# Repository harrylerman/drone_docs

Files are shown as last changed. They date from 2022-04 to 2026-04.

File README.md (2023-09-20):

# drone_docs
Documentation for the Pterosoar drone

Documentation includes: 

    Preflight prep guide: quick guide to ensure compliance with the CARs for every drone flight.

    Normal procedures: Required by CARs. Pre-flight, Takeoff, Launch, Approach, Landing procedures.
    
    Emergency procedures: Required by CARs: Control station failure, equipment failure, RPA failure, Lost Link, Flyaway, Flight Termination procedures. 
  
    TC Drone AIM: Fantastic source of knowledge for drone flying and the regs, doc from TC.

    TC CARs Part IX: Drone CARs.

    Flight log: Logbook form.

    Maintenance log: Logbook form.

    Operations Manual: Required by CARs. Sections: General, Description, Limitations, Hazards-Warnings-Protections, Normal/Emergency procedures, Handling-Care-Maintenance, Supplements/Payloads.
    
    Pos-Alt-Verification (for operations in controlled airspace): Verification of lateral/vertical position accuracy.

    Pos-Alt Addendum: Addendum to the above verification for the new F9P module.

    Mapping procedures: Procedures to follow for each drone mapping outing. 

All documents are based on the CARs Part IX; Standard 922 - RPAS Safety Assurance; Advisory Circular AC-922-01; and the submission site for a drone Safety Assurance.

CARs Part IX: https://lois-laws.justice.gc.ca/eng/regulations/SOR-96-433/FullText.html#s-900.01

Standard 922: https://tc.canada.ca/en/corporate-services/acts-regulations/list-regulations/canadian-aviation-regulations-sor-96-433/standards/standard-922-rpas-safety-assurance-ca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

AC-922-01: https://tc.canada.ca/en/aviation/reference-centre/advisory-circulars/advisory-circular-ac-no-922-001

RPA Safety Assurance submission form: https://tc.canada.ca/en/aviation/drone-safety/help-drone-safety-partners-manufacturers/submit-drone-safety-assurance-declaration-overview

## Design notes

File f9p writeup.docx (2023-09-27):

Dual F9P documentation and testing

Motivation

The need for a dual-GPS heading system stems from our attempts to fly in the Arctic during Summer 2022. The drone was very finicky to arm for flight, it kept cycling between the green “Ready for flight” (armable) status and the yellow “Not ready” (not armable) status. Once flying it behaved very erratically – would not maintain position in Position Mode, and drifted rather violently laterally until it crashed into a building.

Subsequent logfile analysis revealed the “Magnetometer Innovation Test Ratio” far exceeded acceptable values.

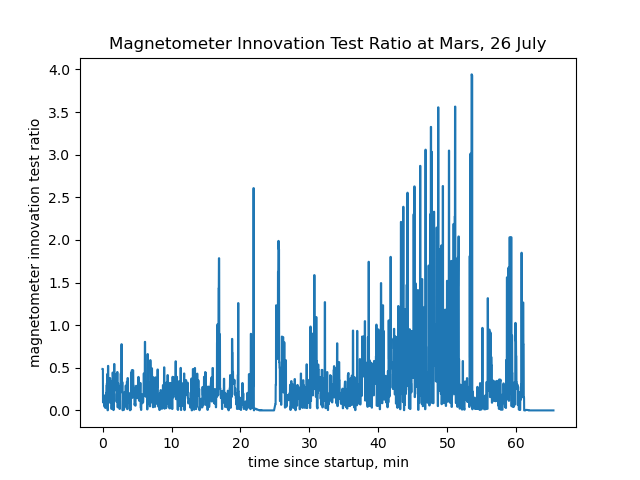
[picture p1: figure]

A brief explanation of this test ratio:

In Kalman filters (https://en.wikipedia.org/wiki/Kalman_filter) which the drone uses for its state estimation (https://docs.px4.io/v1.12/en/advanced_config/tuning_the_ecl_ekf.html), "innovation" has a particular meaning. Here's a wiki link (https://en.wikipedia.org/wiki/Innovation_(signal_processing)) about it. It's similar to a residual, it is the difference between the predicted state at a time t and the actual measured state at time t.

The innovation is the difference between the observed value of a variable at time t and the optimal forecast of that value based on information available prior to time t.

In contrast, the residual is the difference between the observed value of a variable at time t and the optimal updated state of that value based on information available till (including) time t.

The drone calculates its magnetometer innovation and then computes a ratio of the innovation to an "acceptable" level. These quantities are expressed in terms of standard deviations. The acceptable level is set via the "mag_gate" parameter (ctrl-f it here (https://docs.px4.io/main/en/advanced_config/parameter_reference.html)), and is 3 standard deviations by default. The mag ratio should be 0.5 or below at all times (https://mavlink.io/en/messages/common.html):

Under normal operation the innovation test ratios should be below 0.5 with occasional values up to 1.0. Values greater than 1.0 should be rare under normal operation and indicate that a measurement has been rejected by the filter. The user should be notified if an innovation test ratio greater than 1.0 is recorded. Notifications for values in the range between 0.5 and 1.0 should be optional and controllable by the user.

So why were our magnetometer errors so high? It turns out that the magnetic inclination around MARS (https://www.ngdc.noaa.gov/geomag/WMM/image.shtml) is about 88 degrees, ie only 2 degrees off of vertical. That translates to very little signal to the magnetometer. Which motivates the dual GPS system for GPS heading.

Description:

The u-blox F9P GPS module is necessary for dual-GPS heading. Technically the M8P could be used as it supports moving RTK base, but the PX4 firmware would need some hacking to compute the NED components whereas the F9P supplies these components to the FC. We are using two 49g Holybro helical F9P (https://holybro.com/products/h-rtk-f9p-gnss-series)s:

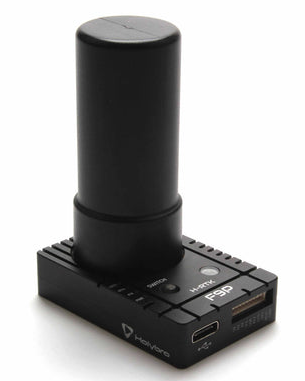
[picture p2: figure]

Dual-F9P system setup

From PX4 site (https://docs.px4.io/v1.12/en/gps_compass/u-blox_f9p_heading.html):

Ideally the two antennas should be identical, on the same level/horizontal plane and oriented the same way, and on an identical ground plane size and shape (Application note (opens new window) (https://www.u-blox.com/sites/default/files/ZED-F9P-MovingBase_AppNote_%28UBX-19009093%29.pdf), section System Level Considerations).

- The application note does not state the minimal required separation between modules (50cm has been used in test vehicles running PX4).
- The antennas can be positioned as needed, but the GPS_YAW_OFFSET (https://docs.px4.io/v1.12/en/advanced_config/parameter_reference.html) must be configured: GPS > Configuration > GPS as Yaw/Heading Source (https://docs.px4.io/v1.12/en/gps_compass/).

In overview:

- The UART2 of the GPS devices need to be connected together (TXD2 of the "Moving Base" to RXD2 of the "Rover")
- Connect UART1 on each of the GPS to (separate) unused UART's on the autopilot, and configure both of them as GPS with baudrate set to Auto. The mapping is as follows:
  - Main GPS = Rover
  - Secondary GPS = Moving Base
- Set GPS_UBX_MODE (https://docs.px4.io/v1.12/en/advanced_config/parameter_reference.html) to Heading (1)
- EKF2_AID_MASK (https://docs.px4.io/v1.12/en/advanced_config/parameter_reference.html) parameter bit 7 must be set (see GPS > Configuration > GPS as Yaw/Heading Source (https://docs.px4.io/v1.12/en/gps_compass/)).
- GPS_YAW_OFFSET (https://docs.px4.io/v1.12/en/advanced_config/parameter_reference.html) may need to be set (see GPS > Configuration > GPS as Yaw/Heading Source (https://docs.px4.io/v1.12/en/gps_compass/)).
- Reboot and wait until both devices have GPS reception. gps status should then show the Main GPS going into RTK mode, which means the heading angle is available.

Note

If using RTK with a fixed base station the secondary GPS will show the RTK state w.r.t. the base station.

In addition to the above parameters, we set the following:

GPS1_config to ‘GPS’

GPS2_config to ‘GPS’

EKF2_mag_type to ‘None’. This removes the magnetometer input from the state estimator.

The heading vector goes from the moving base (connected to GPS 2) to the rover (connected to GPS 1). We have these GPSs aligned back to front, so did not have to configure the GPS_YAW_OFFSET parameter. Here is a page (https://docs.px4.io/v1.12/en/config/flight_controller_orientation.html) I’ve referenced a few times to keep the drone’s reference frame straight in my mind.

Wiring

The rover (front GPS) must connect to GPS1. The moving base (rear GPS) must connect to GPS2.

GPS1 on the Cube Orange is an 8-pin port. GPS2 is a 6-pin port.

Here (https://docs.holybro.com/gps-and-rtk-system/f9p-h-rtk-series/standard-f9p/pinout) is the pinout of the Holybro Helical F9P:

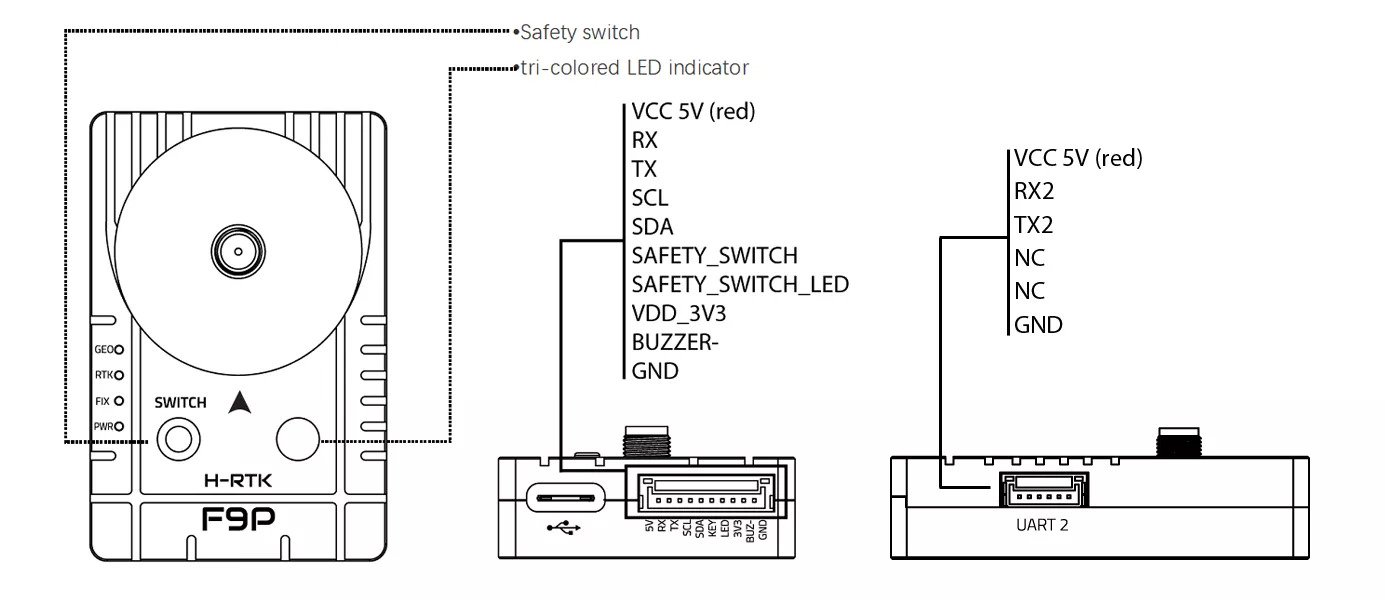
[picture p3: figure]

Note that the main GPS (UART1) port is 10 pins. It is really designed for the newer Pixhawk, like the 6X with the following pinout (https://docs.holybro.com/autopilot/pixhawk-baseboards/pixhawk-baseboard-ports) (perfectly matches the pinout of the Helical):

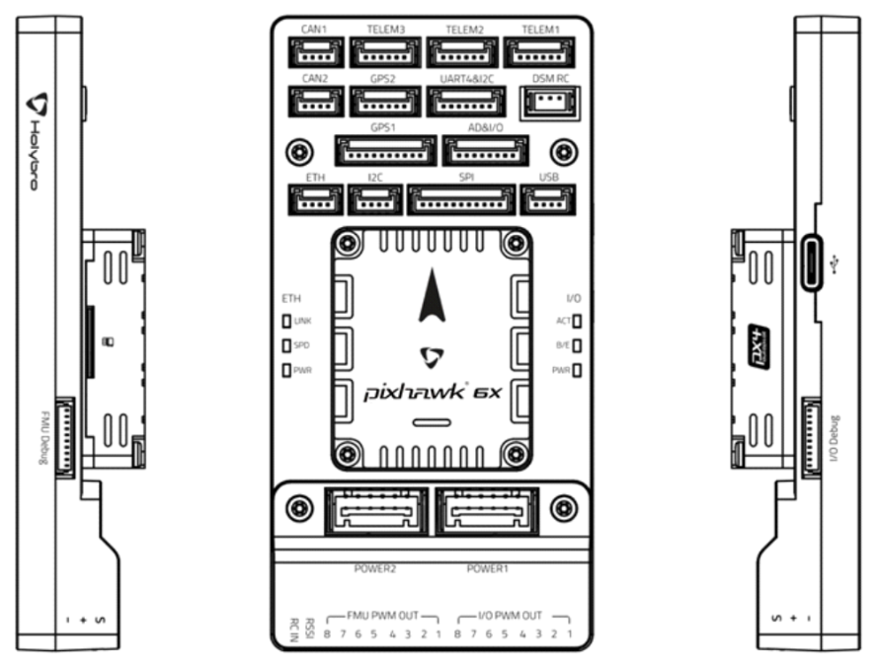
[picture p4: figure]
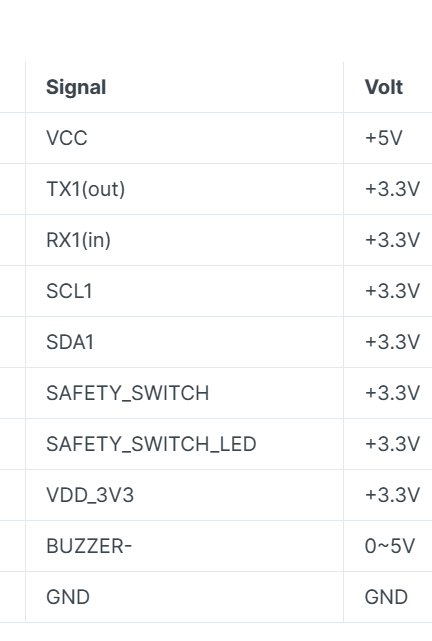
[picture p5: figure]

However, it is still compatible with (https://docs.holybro.com/gps-and-rtk-system/f9p-h-rtk-series/standard-f9p/h-rtk-with-cube-autopilot) the Cube Orange. Here is the Cube Orange pinout for GPS1 and GPS2:

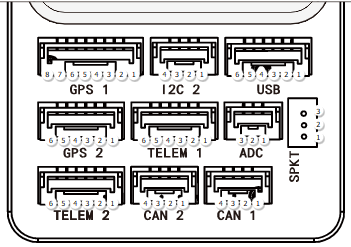
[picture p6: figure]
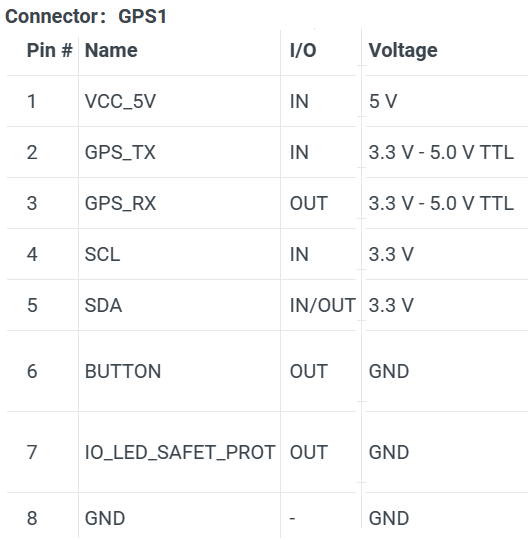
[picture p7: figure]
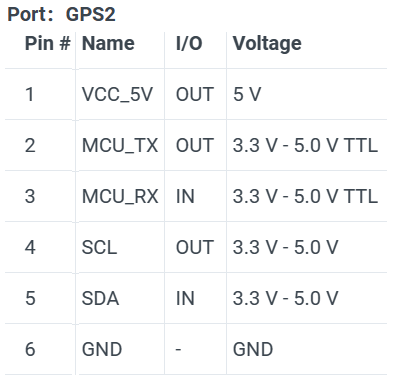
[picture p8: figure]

GPS1 port: Wire the matching connectors from the Holybro to the Pixhawk port (pins 1, 2, 3, 4, 5, 10 from the Holybro to pins 1, 2, 3, 4, 5, 8 on the Pixhawk). The integrated safety switch in the Holybro is not designed for the Cube Orange, it is designed for the 5 or 6x with 3.3V TTL. Also, the Cube Orange has no 3.3 VDD pin, and the buzzer is on the USB connector. So, when connecting the 10-pin Holybro line to the 8-pin Pixhawk port, we leave out the pins for safety switch, safety switch LED, 3.3 VDD, and buzzer (pins 6, 7, 8, 9 on the Holybro side). Would be curious to learn about the decision to move the buzzer from USB to GPS1 between the Cube Orange and 5/6x.

To still use the original safety switch, it can be removed from its default connector by carefully removing the crimped pins 6 and 7 (the two black wires) from the connector, and then de-soldering the splice to pin 1 (5V, red wire). We then insert those crimped connectors into the Pixhawk side of our new GPS line from the Holybro at positions 6 and 7, and splice into pin 1. Or, if that is too much trouble, the button can be disabled via the COM_PREARM_MODE parameter.

GPS2 port: The wiring is similar – do not include pins 6, 7, 8, 9 from the Holybro. GPS2 has no pins for the safety switch so it is not a concern.

UART2 ports: both 6 pin ports, create a line from pin 4 (Tx) of the moving base to pin 5 (Rx) of the rover.

For all of the above, the connector type is JST-GH.

Heading tests on roof

After setting all the parameters and doing all the wiring, we brought the drone up to the roof for some tests. Comparing to a handheld compass, the dual GPS heading seems very accurate, down to a degree or less. This seems to match up with the spec from u-blox (https://www.u-blox.com/en/product/zed-f9p-module) (our baseline is about 67cm):

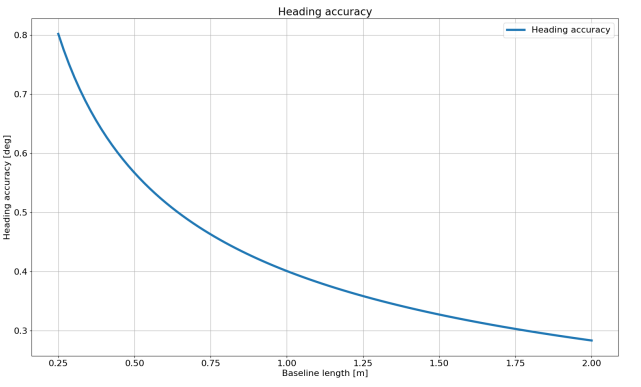
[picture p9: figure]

The resolution seems effectively a degree or less as well. The compass swings very smoothly as the drone is rotated; there is still sensor fusion with the IMUs so this is sensible.

If the drone loses the GPS signal, the heading starts to just swing around in a circle at ~1 deg/sec. But, the drone automatically goes into Altitude Hold mode if it loses GPS, so this isn’t a real danger. There is no indication on the Taranis handheld controller when this happens. There is a text and audio alert from QGC on the laptop.

We wanted to verify that the magnetometer is indeed removed from the state estimator via the EKF2_mag_type parameter. To test this, we waved a magnet next to the drone in the default mode without dual GPS for heading and with the magnetometer enabled. The heading did indeed swing around as the magnet was moved around the Cube Orange. We repeated the test with dual GPS enabled and the magnetometer disabled, and the heading gave no response to the magnet. So hopefully the magnetometer is indeed not included in the state estimator at all.

Hardware mounting

Likely stemming from the ongoing global supply chain issues, 10mm OD carbon fiber tubing of anything greater than 0.5m length is hard to find, and expensive to ship. The Tarot 680 Ironman frame comes with two 10mm OD x 28cm mounting tubes, meant to be held in place by rubber grommets at either end of the frame. They are intended as a gimbal mountpoint for a device such as a camera system. We repurpose these by pulling them out from the drone by approximately 25cm and fixing them in place with 3D-printed mounting brackets. We then 3D-print some mounting platforms for the two GPS units. We had to make sure the mounting platform lowered them below plane of the prop discs.

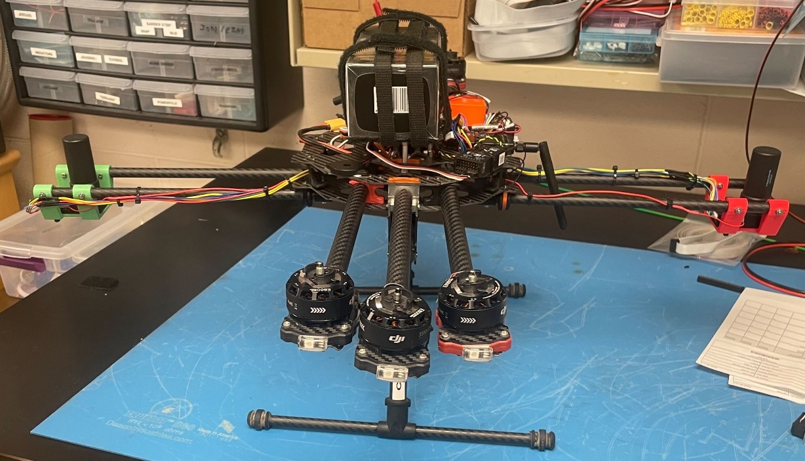
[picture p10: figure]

Drone with dual GPS mounting system. Also visible are the GPS signal lines, and the red line connecting the UART2 ports of the Holybro Helicals.

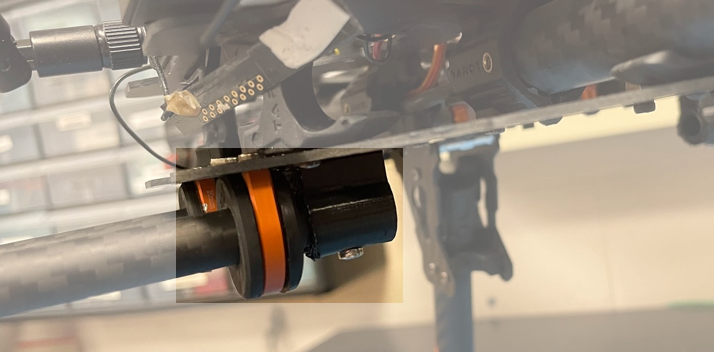
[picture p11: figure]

3D-printed mounting bracket for repurposed Tarot CF tubing (highlighted). The rubber grommets are held by the orange metal brackets.

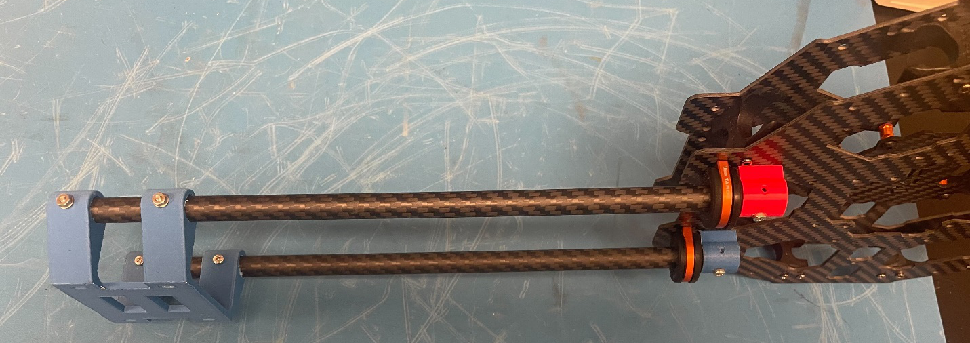
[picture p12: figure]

Some test-printed GPS mounting platforms and CF tubing mounting brackets, included for clarity.

GPS walkaround test for TC

The GPS walkaround test for lateral accuracy verification occurred on March 27, 2023. Details can be found in the memo “Pos-Alt-Addendum.” The GPS system was found to have an accuracy, to a 95% confidence level, of 2.0 m +/- 1.4 m.

First Flight

First flight with the dual-F9P GPS system occurred on March 28, 2023. There were no issues with the drone’s performance – if anything, it seems to fly more stably with the dual GPS system than with the magnetometer (qualitative observation).

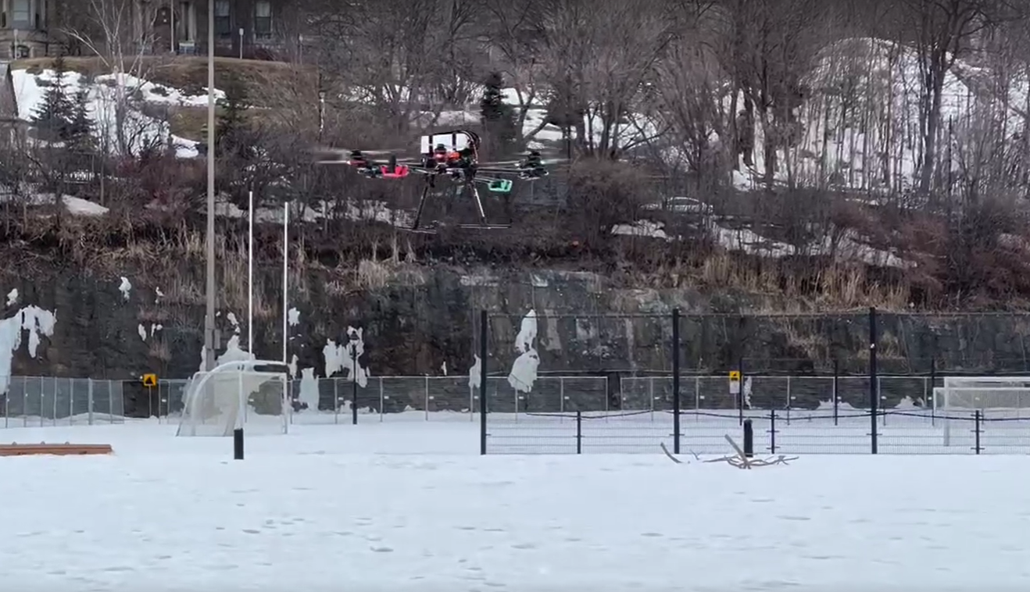
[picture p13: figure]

Coming in for a landing at the conclusion of the first flight of the dual-GPS system.

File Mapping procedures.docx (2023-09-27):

16 Sep 2023

Larry Herman

Drone mapping procedures

Tools to bring on every mapping flight:

- SMA wrench
- Multi-tool
- Digital Multimeter
- Small screwdriver and allen key for drone bolts
- Drone rescue kit
- Spare props
- FieldFox (optional)
- Drone and usual equipment/payload

Items to bring if setting up an LWA and operating without an established ALBATROS station (ie soccer field ops):

- LWA
  - Topper
  - Hardware
  - Petals
  - Central fiberglass supports and flange
  - Central pole
  - Base (ie Xmas tree stand)
- FEE (with optional spare)
- Driver screwdrivers for LWA (2 sizes)
- Readout SNAP box with appropriate RF chain
- Hard drive if not internal to the SNAP box
- RF rescue kit (attenuators mainly)
- GPS antenna
- Batteries with cables (jumper and power cable to readout box)
- Coax cables
  - Riser cables for LWA central pole
  - Long cables from LWA to SNAP box

Setup instructions for flying without an established ALBATROS station (ie soccer field ops):

- Determine location of readout system and crew (ie picnic table)
- Determine location of LWA
  - Can uncoil coax cable and use its length to determine this
- Set up LWA with Xmas tree stand base
  - Includes connecting riser cables to FEE
- Jumper batteries and hook up power cable for the readout box (do not plug in readout box yet)
- Connect GPS antenna to readout box
- Connect hard drive to readout box if needed
- Connect coax cables to LWA riser cables and readout box
- Power on readout box
  - Ensure drone config file is in the new_daq directory and named “config.ini”
  - Ensure drive mounts and dump_baseband and dump_spectra run.
- Power off readout box.

Readout system should now be ready for drone operations.

***From here on the instructions are applicable with or without a full ALBATROS station***

- Perform normal drone preflight procedures.
- Check all accessible SMA connectors on the drone’s payload before and after every flight.

The following are general procedures to perform a complete series of mapping sorties. Flights can be tailored to specific needs of each mapping outing.

- Use the drone to measure the antenna’s lat/lon. Record this.
- Create a flightplan with the drone hovering directly over the antenna for 5 minutes at altitude (ideally 200 ft). Upload flightplan to the drone.
- Power on the transmitter but not the chopper.
- Have the drone takeoff and perform the flight (this is the “cal flight”).
- With the drone hovering over the antenna, power on the readout system and allow to autotune.
- Once autotuning is complete, take control of the drone in position mode and hand-fly to a landing.
- Check ADC bit numbers.
  - May need to tune the RF chains or the drone’s emitter
  - Repeat the cal flight as necessary.
- Power on the chopper.
- Perform the following flights (use saved MARS flightplans as references, flightplans can and should be created ahead of time and the pattern simply moved to the measured antenna position on-site). There will probably need to be 2-3 breaks to charge drone batteries (can take up to 1.5 hours):
  - Star pattern used for a quick check (~6 mins).
  - Center beam raster (~30 mins).
  - Orthogonal center beam raster (~30 mins).
    - Probable battery charge break here (~1.5 hrs).
  - Side-lobe raster (larger pattern but more spaced out, ~30 mins).
  - Orthogonal side-lobe raster (~30 mins).
    - Probable battery charge break here (~1.5 hrs).
  - “Disco ball” and roll/pitch flight: hover the drone at various positions and altitudes, yaw the drone 360 degrees and move the drone laterally to make it roll/pitch, this is to check polarization effects (~5 mins).
  - Re-do the cal flight with the emitter and chopper powered off. This is in preparation for the following drone RFI flight.
  - Drone RFI flight: flight with emitter/chopper powered off to try to gauge the drone’s own RF output. Fly either a simple cross or star pattern as time/battery permits.
- Power down / cleanup.

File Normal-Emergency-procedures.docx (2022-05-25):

Normal Operating Procedures

Ref: 901.23 No pilot shall operate a remotely piloted aircraft system unless the following procedures are established:

- normal operating procedures, including pre-flight, take-off, launch, approach, landing and recovery procedures.

Pre-Flight Procedures:

- Follow the pre-flight planning guide.
- Brief flight crew or visual observers of any duties they are to perform or any other information relevant to the flight.
- Determine the acceptability of actual and developing weather conditions for flight.
- Organize and arrange material and equipment in a manner that makes the items readily available.

Take-off Procedures:

- Complete all preflight procedures and visual inspections.
- Ensure the selected take-off site is clear of obstacles and personnel.
- Command the drone to take-off to an appropriate altitude.
- Ensure the drone lifts off and climbs away in a controlled and stabilized manner.
- Note the take-off time.

Launch Procedures:

N/A, no launch system will be utilized.

Approach Procedures:

- Command the drone to proceed to overhead the intended point of landing.
- Ensure the drone approaches overhead the intended point of landing in a controlled and stabilized manner, and slows so as not to overshoot the landing site.
- Ensure obstacle and personnel clearance as the drone approaches overhead the intended point of landing.

Landing Procedures:

(Recovery procedures: N/A, no recovery system will be utilized.)

- Ensure the intended point of landing is clear of obstacles and personnel.
- Ensure the drone is overhead the intended point of landing.
- Command the drone to descend to the landing site.
- Ensure the drone descends at an appropriate rate in a controlled and stabilized manner.
- Note the time of landing and secure the drone.

Emergency Procedures

Ref: 901.23 No pilot shall operate a remotely piloted aircraft system unless the following procedures are established:

- emergency procedures, including with respect to: a control station failure, an equipment failure, a failure of the remotely piloted aircraft, a loss of the command and control link, a fly-away, and flight termination.

Control Station Failure Procedures:

If the failure is on the part of the ground station (i.e. laptop with QGroundControl):

- Immediately take manual control with the handheld transmitter (i.e. the Taranis).
- Once stabilized, command the drone to altitude or position hold as appropriate.
- Attempt to troubleshoot the ground station failure.
- Assess the ability to continue the flight. If unable, discontinue the flight and land.

If the failure is on the part of the handheld transmitter (i.e. the Taranis):

- Maintain positive control of the drone via the ground station.
- Attempt to troubleshoot the handheld transmitter failure.
- If unable to regain functionality of the handheld transmitter, discontinue the flight and land.

Equipment Failure Procedures:

- Assess the nature of the equipment failure.
- If the pilot and crew determine the equipment failure to be a danger to safety of flight – land immediately (examples of equipment failure that could impact safety of flight: GPS failure, power system failure, radio failure).
- If the pilot and crew determine that safety of flight is not impacted, assess the controllability of the vehicle. If controllability is in doubt – land immediately (examples of equipment failure that could impact controllability: intermittent Holybro or X8R radios, motor failure).
- If the pilot and crew determine that the flight can be continued, assess the impact of the equipment failure on the mission. Alter mission profile as necessary.

Failure of the Remotely Piloted Aircraft Procedures:

- Maintain visual contact with the drone.
- Identify and record the drone’s present position.
- Attempt to maintain control of the drone via any control link (i.e. handheld transmitter or ground station) in any flight mode.
- Attempt to ensure objects and personnel remain clear of potential drone impact.
- Note the position and time of drone impact as applicable.
- Notify the appropriate control facility as applicable.
- File a drone incident report with Transport Canada / TSB as applicable.

Loss of Command and Control Link Procedures:

- Be prepared to take control immediately if at any time the link is restored. Consider landing immediately in this case.
- Maintain visual contact with the drone.
- Identify and record the drone’s present position.
- Attempt to regain control of the drone via any control link (i.e. handheld transmitter or ground station) in any flight mode.
- Select an altitude and power setting appropriate for the lost link situation.
- Attempt to troubleshoot the lost link, being sure to consider both the handheld transmitter and the ground control station.
- Perform “fly-away” emergency procedure as applicable.
- Notify the appropriate control facility as applicable.
- File a drone incident report with Transport Canada / TSB as applicable.

Fly-Away Procedures:

Perform the following tasks without undue delay:

- Identify and record the drone’s present position.
- Identify and record the direction and altitude the drone was last seen travelling.
- Estimate the approximate available flight time that will remain with the fuel/power on board upon arrival at the destination (Example: 15 minutes).
- Comply with “Loss of Command and Control Link” procedures.
- Consider flight termination procedures.
- Without delay contact the appropriate control facility to provide information on the “fly away” as applicable.
- File a drone incident report with Transport Canada / TSB as applicable.

Flight Termination Procedures:

Flight termination is a last-resort emergency option to end the drone flight immediately. All motors will cease operation and the drone will fall uncontrolled from its current position to the ground as the flight computer simultaneously turns off all controllers and sets all PWM outputs to their failsafe values. Note that there is no way to recover from a flight termination once it is triggered – the vehicle requires a hard reset by disconnecting power before it can be used again.

Consider the following before a flight termination:

- The safety of personnel and objects in the vicinity of the drone’s impact site.
- Damage that will result to the drone as a result of the flight termination.
- If flight termination is triggered, file a drone incident report with Transport Canada / TSB as

applicable.

Emergency Contact Information:

Transport Canada Aviation Operations Center 24/7 emergency number (for an imminent and immediate threat to aviation and public safety): 1-877-992-6853

https://tc.canada.ca/en/aviation/aviation-accidents-investigations/emergencies-incident-reporting

Nav Canada 24/7 Flight Operations number (for immediate relay to control facilities): 1-866-WX-BRIEF (1-866-992-7433).

Montreal (CYUL) Tower: 514-633-3312 (Primary) / 514-633-3311

Montreal ACC direct line: 1-800-633-1353.

Quebec FIC direct line: 1-866-541-4105.

VHF/UHF guard frequencies (to attempt to reach any control facility or aircraft in range who may be able to relay information): 121.5/243.0 MHz

Transport Canada drone incident report: https://tc.canada.ca/en/aviation/drone-safety/report-drone-incident

For an incident involving serious injury or death or midair collision, also report to the Transportation Safety Board via phone at 819-994-3741 / 1-800-387-3557 as well as online:

https://www.tsb.gc.ca/eng/incidents-occurrence/aviation/index.html

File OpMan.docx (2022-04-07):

### Pterosoar Operating Manual

### Table of contents

Section 1: General

Section 2: Description

Section 3: Operating limitations

Section 4: Hazards, Protections, and Warning Systems

Section 5: Normal and Emergency Operating Procedures

Section 6: Handling, Care and Maintenance

Section 7: Supplements and Payloads

## Section 1

### General

#### Table of contents

1.1 Introduction

1.2 Warnings, Cautions, and Notes

1.3 List of Definitions and Abbreviations

1.3.1 Abbreviations and Acronyms

1.3.2 Definitions

### 1.1 Introduction

### This Section provides basic data and information of general interest. It also contains definitions or explanations of symbols, abbreviations, and terminology commonly used.

### 1.2 Warnings, Cautions and Notes

The following definitions apply to warnings, cautions, and notes used in this RPAS operating manual:

Warning: An operating procedure, practice, or condition, etc., that may result in injury or death if not carefully observed or followed.

Caution: An operating procedure, practice, or condition, etc., that may result in damage to equipment if not carefully observed or followed.

Note: An operating procedure, practice, or condition, etc., that must be emphasized.

### 1.3 List of Definitions and Abbreviations

#### 1.3.1 Abbreviations and Acronyms

C2: Command and Control

DOP: Dilution of Precision

EMI: Electromagnetic interference

ESC: Electronic Speed Controller

GNSS: Global Navigation Satellite System

GPS: Global Positioning System

GSE: Ground Support Equipment

HITL: Human in the loop

HOTL: Human on the loop

IMU: Inertial Measurement Unit

LiPo: Lithium Polymer

PBM: Power Brick Mini

PDB: Power Distribution Board

QGC: QGroundControl

RPA: Remotely Piloted Aircraft

RPAS: Remotely Piloted Aircraft System

RSSI: Received signal strength indication

RTK: Real-time kinematics

VFR: Visual Flight Rules

VLOS: Visual Line of Sight

#### 1.3.2 Definitions

As may be applicable, add here as needed.

## Section 2

### Description

### Ref: 901.78 A manufacturer that has made a declaration to the Minister in respect of a model of remotely piloted aircraft system under section 901.76 shall make available to each owner of that model of system

### (c) a remotely piloted aircraft system operating manual that includes

### (i) a description of the system

#### Table of contents

2.1 Introduction

2.2 Physical Description of the RPA

2.2.1 Three-View of the RPA

2.2.2 Airframe

2.2.3 Dimensions

2.3 Flight Controls

2.4 Propulsion System

2.4.1 Motor | Propeller | Electronic Speed Control

2.4.2 Battery

2.5 Electrical System

2.6 Avionics System

2.6.1 Navigation

2.6.2 Telemetry

2.6.3 Command and Control Link

2.7 Remote Pilot Station

2.8 Firmware | Software

2.9 Ground Support | Surveillance

### 2.1 Introduction

This Section provides a detailed description of the RPAS and its Systems. Some equipment or payload described may be optional and as such not installed in the RPA. Refer to Section 7 for details of other optional equipment or payload.

### 2.2 Physical Description of the RPA

Airframe Type: Hexacopter

A primarily carbon-fiber construction RPA used for radio science work (mainly antenna calibration) at McGill University.

Built by: Larry Herman, McGill University, Montreal, QC, Canada.

#### 2.2.1 Three-View of the RPA

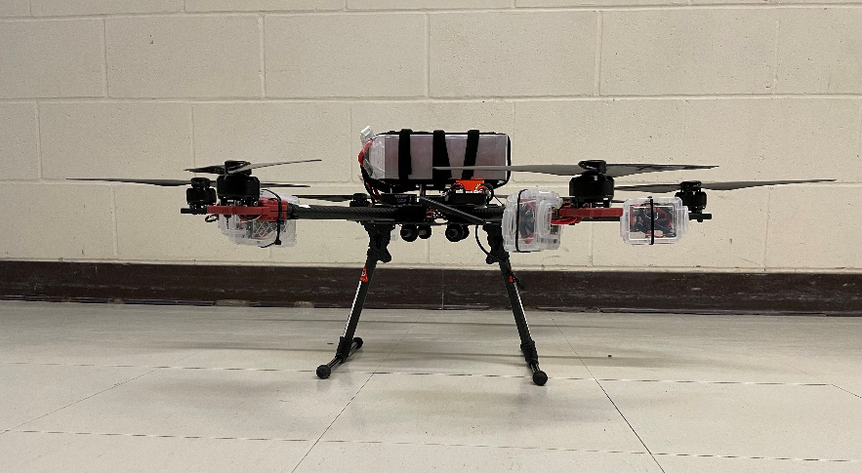
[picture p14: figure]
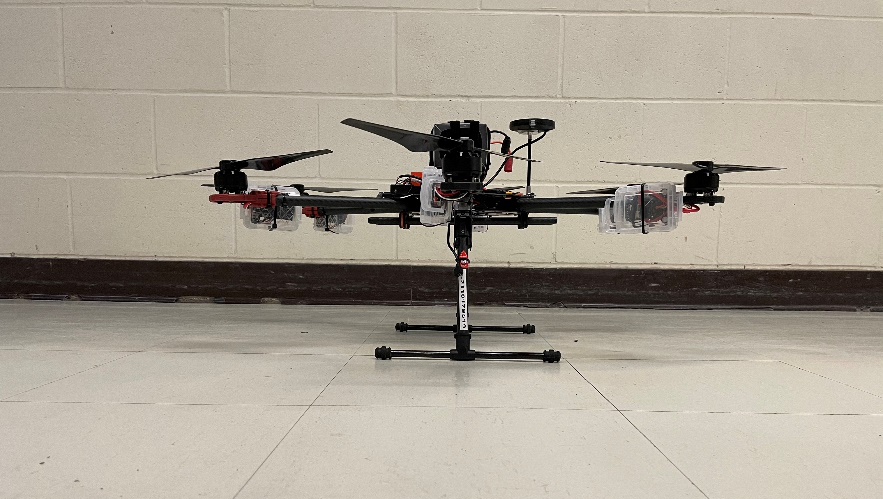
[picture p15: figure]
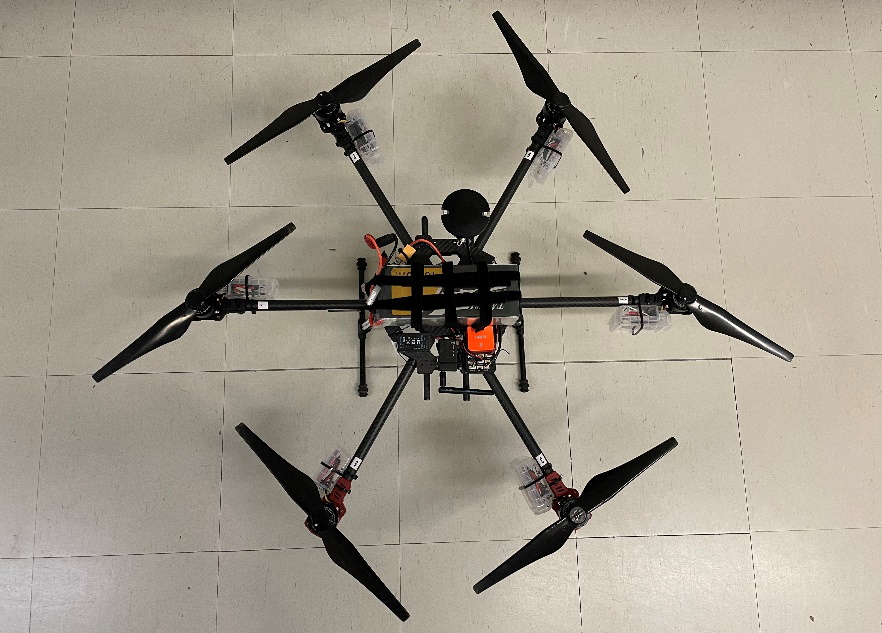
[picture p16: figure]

#### 2.2.2 Airframe

#### Pterosoar incorporates a Tarot Iron Man 680 carbon-fiber frame.

#### 2.2.3 Dimensions

Overall Dimensions: 1015mm x 1015mm x 330mm

Important Dimensions:

#### Motor-to-motor diameter: 685mm

#### Height from ground to lower rods: 180mm

#### Height from ground to top of frame: 220mm

Propeller diameter: 13in

### 2.3 Flight Controls

Pterosoar uses a FrSky Taranis X9D Plus 2019 handheld controller for manual control. For automated control, a groundstation consisting of a laptop running QGroundControl communicates with the RPA via a telemetry system. The method of flight control is conventional: the Pixhawk Cube Orange flight controller varies each motor’s speed to produce the total required torque and thrust to achieve the desired attitude, altitude, and velocity.

### 2.4 Propulsion System

#### 2.4.1 Motor | Propeller | Electronic Speed Control

Motors

Number of Motors: 6

Motor Manufacturer: DJI

Motor Model Number: 3510H

Motor Type: Brushless

Motor Power Rating: 420 KV

Propellers

Number of Propellers: 6

Propeller Manufacturer: DJI

Propeller Model Number: 1345S

Number of Blades: 2

Propeller Type: Fixed pitch

Electronic Speed Controls

Number of ESCs: 6

ESC Manufacturer: DJI

ESC Model Number: Inspire 1

ESC Type: PWM

ESC Power Rating: 26V, 20A

#### 2.4.2 Battery

Battery Manufacturer: Tattu

Battery Type: 6S LiPo

Number of batteries required for flight: 1

Number of spare batteries required (available) on site: Mission-dependent

See Section 3.7 for battery limitations.

#### 2.5 Electrical System

The Pterosoar 6S LiPo battery has a maximum voltage of 3.3V – 4.2V per cell. The battery connects directly to a Power Brick Mini (PBM) power supply via AS150 and XT60 connectors. The PBM supplies full battery voltage to the Power Distribution Board (PDB), and stepped-down 5V power to the Pixhawk Cube Orange flight controller. The PDB supplies electrical power to the motors and ESCs. The flight controller supplies electrical power to all other components.

### 2.6 Avionics System

The primary component of the Pterosoar avionics system is the Pixhawk Cube Orange flight controller. Internal Pixhawk sensors include 3 accelerometers, 3 gyroscopes, 1 compass, and 2 barometric pressure sensors. All other flight-related sensors and radios connect directly to the Pixhawk.

Key features of the Pixhawk:

32bit STM32H743ZI (32bit ARM Cortex M7 (https://en.wikipedia.org/wiki/ARM_Cortex-M), 400 MHz, Flash 2MB, RAM 1MB)

32bit STM32F103 failsafe co-processor

14 PWM / Servo outputs (8 with failsafe and manual override, 6 auxiliary, high-power compatible)

Abundant connectivity options for additional peripherals (UART, I2C, CAN)

Redundant power supply inputs and automatic failover

External safety switch

Multicolor LED main visual indicator

High-power, multi-tone piezo audio indicator

microSD card for high-rate logging over extended periods of time

Below is a diagram of the Pixhawk Cube Orange with all other flight-related components connected. These components are discussed in more detail elsewhere in this Section.

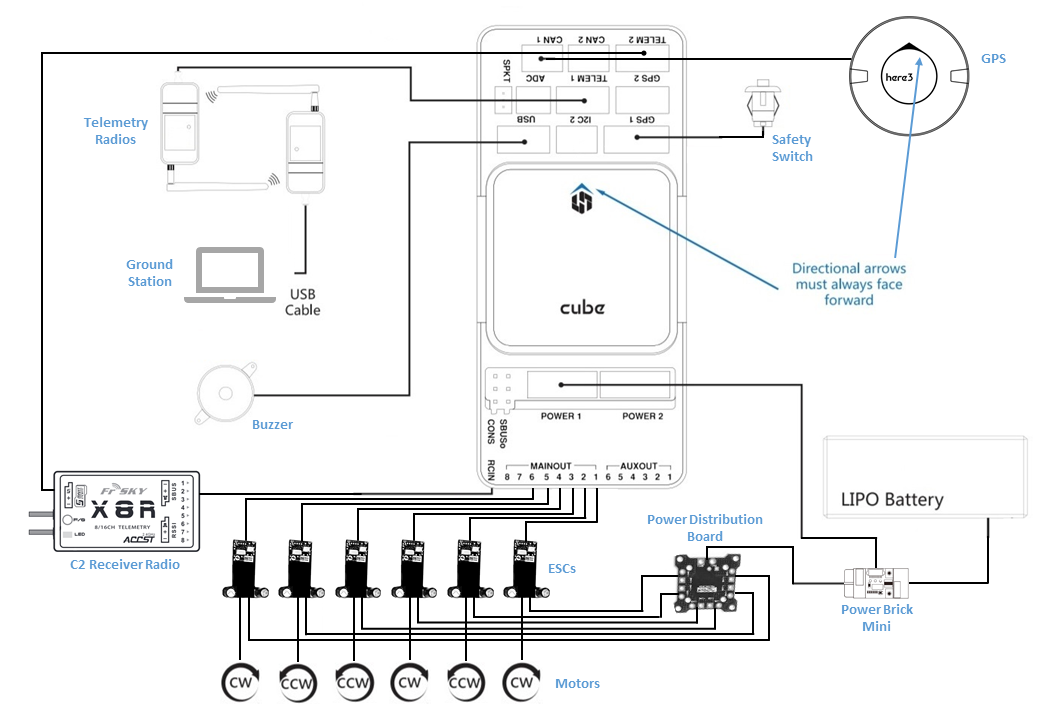
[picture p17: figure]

All sensors and antennas are mounted directly on the central platform, with the exception that one blade antenna from the X8R radio is mounted on arm #1.

#### 2.6.1 Navigation

The Pixhawk Cube Orange flight controller also functions as the autopilot. It is a digital, solid-state system that accepts pre-programmed flight plans uploaded from QGroundControl. It controls the RPA via the conventional flight control system, varying motor speeds to produce the desired torque and thrust to control attitude, altitude, and velocity.

The Pixhawk employs an Estimation and Control Library (ECL) which utilizes an Extended Kalman Filter (EKF) algorithm to process sensor inputs and compute the position state of the RPA. Sensors incorporated into the EKF state estimation include the GPS, IMU, magnetometer, and internal barometric pressure sensor.

Pterosoar’s navigation system includes two separate GPS systems.

The primary GPS system is the Here3 GPS. In the default mode, with a 3D lock the Here3 has an accuracy of +/- 2.5m in any direction. When using the base station for RTK performance, the accuracy is +/- 0.025m in any direction.

The secondary GPS is the Radiolink M8N GPS SE100. The M8N has an accuracy of 0.5m.

#### 2.6.2 Telemetry

Pterosoar uses Holybro SiK Telemetry V3 radios. Telemetry is streamed to the laptop base station running QGroundControl.

Specifications:

Output power: 100mW

Operating frequency: 915MHz

Firmware: Open-source SIK

2.6.3 Command and Control Link

Control via the laptop base station running QGroundControl, as well as wireless flightplan upload for autonomous operation, is conducted via the 915MHz telemetry radios.

Manual control is conducted via the FrSky Taranis X9D Plus SE 2019 handheld controller. Specifications:

Output power: 32mW

Operating Frequency: 2.4GHz

Firmware: Open-source OpenTX

The Taranis X9D and the RPA communicate via a FrSky X8R radio. Specifications:

Output power: 39mW

Operating Frequency: 2.4GHz

Firmware: FrSky ACCST D16

2.7 Remote Pilot Station

The groundstation uses QGroundControl on a laptop with standard keyboard and trackpad. The health and status of the RPA is displayed at the top of the main screen. Navigation information, including a real-time depiction of the RPA on a map, and flight plan information is the main element of the home screen of QGC, as shown below.

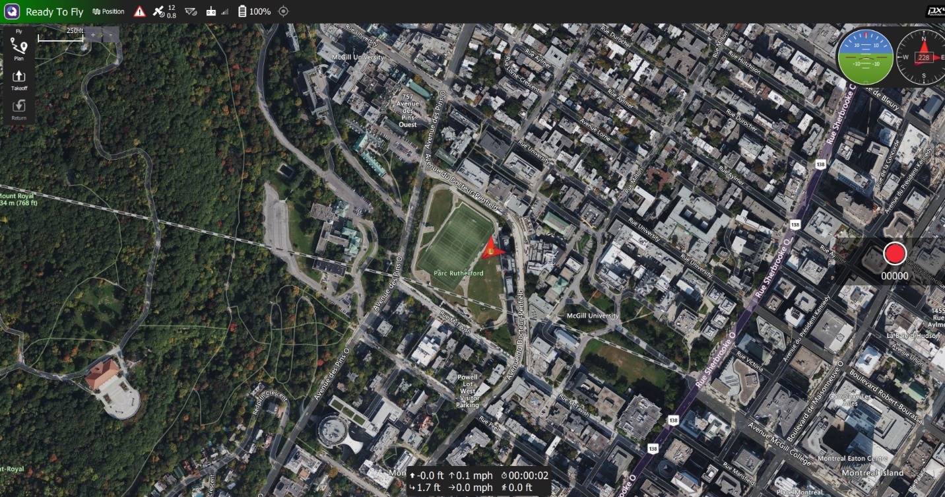
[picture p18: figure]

The Taranis X9D controller has the following switch layout:

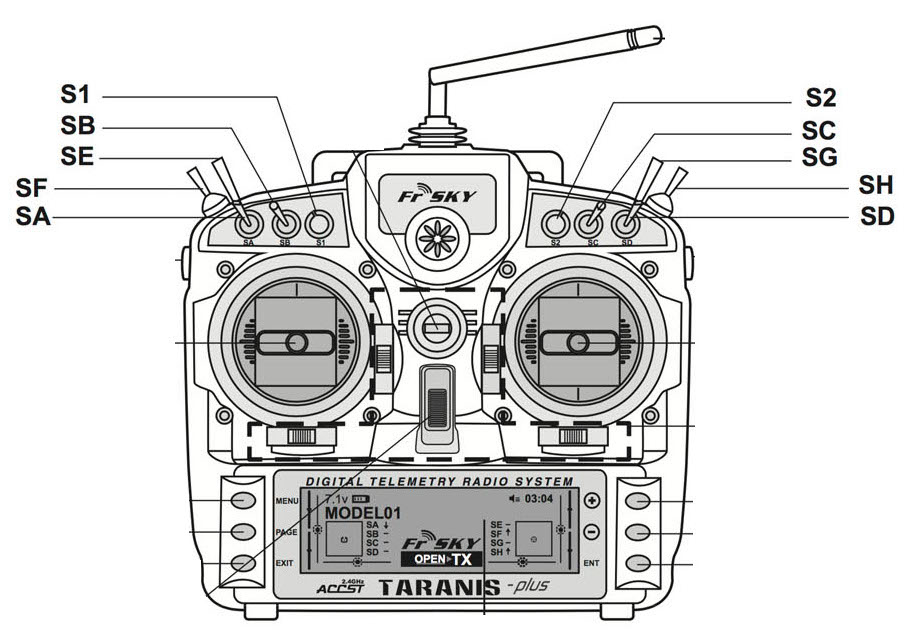
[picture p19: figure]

The controller is configured such that the left stick controls thrust and yaw, and the right stick controls lateral motion (Mode 2).

The primary flight mode switch is SA, and it’s 3 positions are assigned to Altitude (Alt Hold) (up), Position (Pos Hold) (middle), and Mission (Auto) (down). When SC is up, it overrides to Manual mode (this may only be for testing). Moving SE to middle/down will override to Return (RTL). Moving SF to down will override to Land. SC middle/down, SE up, and SF up are all inactive positions.

The main telemetry screen of the Taranis X9D has been configured to show the following information:

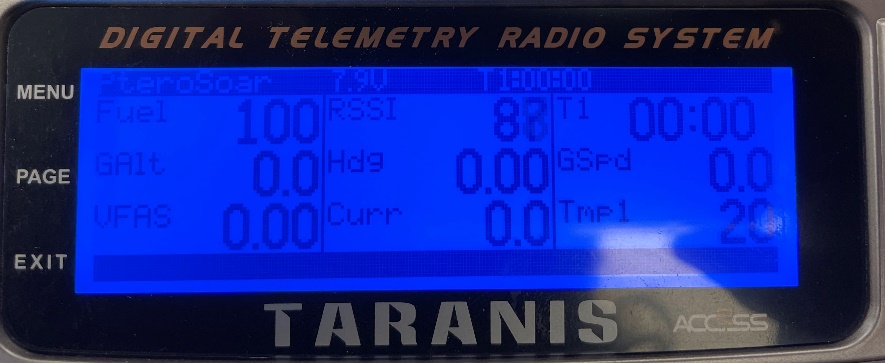
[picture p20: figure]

### 2.8 Firmware | Software

### QGroundControl: Version 4.1.3

### FrSky Taranis X9D: OpenTX version 2.3.12

### Pixhawk: PX4 version 1.12.3

### Holybro SiK telemetry radio: SiK version 2.1

### FrSky X8R radio: ACCST D16 version 2.1.0

### Here3 GPS: version 1.6

### 2.9 Ground Support | Surveillance

No specific GSE is required for the Pterosoar. The RPA must be flown within visual LOS.

## Section 3

### Operating limitations

### Ref: 901.78 A manufacturer that has made a declaration to the Minister in respect of a model of remotely piloted aircraft system under section 901.76 shall make available to each owner of that model of system

### (c) a remotely piloted aircraft system operating manual that includes

(ii) the ranges of weights and centers of gravity within which the system may be safely operated under normal and emergency conditions and, if a weight and center of gravity combination is considered safe only within certain loading limits, those limits and the corresponding weight and center of gravity combinations,

(iii) with respect to each flight phase and mode of operation, the minimum and maximum altitudes and velocities within which the aircraft can be operated safely under normal and emergency conditions,

(iv) a description of the effects of foreseeable weather conditions or other environmental conditions on the performance of both the system and the pilot

#### Table of contents

3.1 Introduction

3.2 Weight | Center of Gravity Limits

3.2.1 Weighing Procedures

3.2.2 Weights

3.2.3 Center of Gravity

3.3 Altitude Limitations

3.4 Velocity Limitations

3.5 Weather Limitations and Effects on System and Pilot

3.6 Kinds of Operation

3.6.1 Operations in Controlled Airspace

3.6.2 Modes

3.7 Battery Limitations

3.8 Range and Endurance Limitations

3.8.1 Battery

3.8.2 Command and Control Link

### 3.1 Introduction

This Section includes operating limitations which are necessary for the safe operation of the RPAS, its motors, standard equipment and standard payload. All information and limits in this Section apply to both normal and emergency conditions.

Warning: All limitations given in this Section must be complied with for all operations.

Note: Refer to the Supplements, Section 7 of this operating manual for information regarding specific equipment or payload.

### 3.2 Weight | Center of Gravity Limits

To obtain the performance, flight characteristics, and safe operation described in this RPAS operating manual, the RPA must be operated within the permissible weight and center of gravity limitations specified in this Section.

### 3.2.1 Weighing Procedures

For weighing, the RPA should be placed in the normal ground position in the center of the scale.

#### 3.2.2 Weights

Basic Weight (including battery): 3.82 kg

Maximum Take Off Weight: 6.30 kg

Maximum payload: 2.48 kg

Warning: Exceeding weight limitations may lead to overloading of the RPA structure and cause loss of control of the RPA and/or structural damage.

#### 3.2.3 Center of Gravity

Pterosoar is a hexacopter with very long moment arms relative to the width of the central platform. The moment arm of any motor to the geometric center of the RPA is 342.5mm, compared to the width of the central platform of 175mm. As a result, components of typical drone equipment weights essentially cannot result in a limiting-case balance condition.

The heaviest component is the battery which is mounted on-centerline at the geometric center of the RPA and as such cannot produce an unbalanced condition. The next heaviest component is the Pixhawk Cube Orange which weighs 73g. Any component weighing less than 73g is considered safe to mount to the central platform without encroaching any limiting-case balance condition.

Any payload must be mounted on-centerline of the central platform. Payloads must be attached to the drone in such a manner that they cannot move or swing dynamically (i.e., no pendulum-style payloads that can swing freely). The flight controller has not been tested with such dynamically movable payloads.

Warning: Exceeding the center of gravity limitations reduces the maneuverability and stability of the RPA.

### 3.3 Altitude Limitations

Maximum altitude: 400 ft AGL or 100 ft above a structure when within 200 ft horizontally from the structure.

Maximum base station altitude: 10,000 ft MSL.

Note: During extended operations, the local barometric pressure (i.e. the local altimeter setting) can change significantly. During such operations, update the QNH barometric altimeter parameter or cycle flight controller power prior to each flight.

### 3.4 Velocity Limitations

Maximum horizontal speed: 20 m/s

Maximum takeoff vertical speed: 5 m/s

Maximum landing vertical speed: 1 m/s

Note: The above limits are based on maximum allowable parameters in QGC and demonstrated performance.

Caution: Maneuver speed and Vne have not been measured. Avoid abrupt control inputs.

3.5 Weather Limitations and Effects on System and Pilot

Wind

Wind limitations: 10 kts sustained, 15 kts gusting.

It is expected that operators have a clear understanding of the effect of wind on aviation, and that flying in wind will have operational effects. In automated (HOTL) flight modes including pre-programmed flight path, automated takeoff, automated landing, or RTH, the RPA will fly against the wind to maintain it’s desired position or flight path. The same is true of semi-automated (HITL) modes including position or altitude hold. In manual mode, the operator must be aware of the winds and make the appropriate inputs to counteract them. In all cases, the effects of flight against the wind on battery endurance should be considered.

Caution: In manual flight mode, flight against winds aloft may increase pilot fatigue.

Temperature

Ambient temperature operating range: 0°C to 40°C

Caution: Consideration should be given to the effects of ambient temperature on pilot fatigue.

Air density

Air density is an important factor in rotary-wing aircraft operations as it directly impacts the generation of lift. Consideration should be given to the density altitude at the time of flight. If the density altitude for the given conditions is abnormally high and aircraft performance seems affected (excess thrust required for takeoff or to maintain altitude), consider aborting the flight.

Caution: Also consider the effects of abnormally high density altitudes on pilot fatigue.

Precipitation

Flight in any form of precipitation is prohibited.

Vibration

Vibrations generally result from the operation of the RPA itself. The Pixhawk flight controller includes vibration isolation on two of the IMU's, with a third fixed IMU as a reference / backup.

Icing

Flight is prohibited when icing conditions are observed, are reported to exist or are likely to be encountered along the route of flight. Flight is prohibited with frost, ice or snow adhering to any part of the RPA.

Electromagnetic Environment

Consider the effects of electromagnetic interference (EMI) from nearby sources such as cell towers, microwave radio relays, or Wi-Fi transmitters. If any interference with the telemetry or C2 link is suspected, abort the flight until the interference is eliminated.

It is strongly suggested to know the KP index expected on the day of the flight. This is the index used to express the magnitude of geomagnetic storms. The scale of the KP index ranges from 0 to 9. It is strongly discouraged to fly a drone when the KP index is between 4 and 9 as this indicates a geomagnetic storm. A geomagnetic storm interferes with the drone's GPS positioning.

3.6 Kinds of Operation

RPAS flights are limited to Visual Line of Sight (VLOS) flights, under DAY Visual Flight Rules (VFR) conditions.

Night flight is prohibited.

#### 3.6.1 Operations in Controlled Airspace

Operations in controlled airspace require an advanced drone pilot certificate and filing with Nav Canada.

Required Accuracy

(1) The remotely piloted aircraft system must have a lateral position accuracy of at least +/- 10m while operating within the controlled airspace.

(2) The remotely piloted aircraft system must have an altitude accuracy of at least +/- 16m while operating within the controlled airspace.

Pterosoar has demonstrated that it meets these accuracy requirements. Results of GPS/altitude verification testing are on file.

The following GPS error considerations should be taken into account during flight operations:

Errors. Accuracy is a probabilistic measurement based on assumptions related to the quality and integrity in a constantly changing environment. It is important to understand the errors that may contribute to degradation of accuracy and take these into account as part of the overall design error budget. Examples of sources of errors adversely affecting accuracy are identified below.

Terrain Errors. GNSS signals are also subject to errors caused by the terrain. Terrain masking of the signal, for example by a building or mountain, blocks the antenna on the RPAS from receiving the satellite signal. A GNSS signal reflected by the landscape such that the receiver now receives "additional" signals which can create confusion and may need to be processed out to avoid creating position errors.

Atmospheric Errors. Atmospheric errors are caused by the Ionosphere and the Troposphere, which are both capable of refracting GNSS radio signals. Ionospheric Density is diurnally dependent, which means that it varies with time of day (or night). The density is affected by, among other factors, humidity, temperature and pressure. These variations adversely affects the "signal speed x time" equation built into GNSS position calculations. To correct for these errors, a number of steps are taken. Troposphere errors can be caused by moisture absorbing/refracting signal and cause errors up to 6m. Ionosphere errors can be caused by the atmospheric refraction of the GNSS signals and may be up to 40-60 m by day and 6-12 m at night. These errors can be mitigated by the use of multi-frequency receivers, selection of masking angle, and/or the use of augmentation systems (either ground-based, such as Local Area Augmentation System [LAAS], or space-based, such as European Geostationary Navigation Overlay Service [EGNOS]).

Satellite Errors. These are errors resulting from poor or unexpected geometries related to the positions of the GNSS satellites in reference to an RPAS. Gravitational effects of the Sun and Moon may pull the SV from planned orbital path. Solar Radiation creates EMI prior to the signal hitting the atmosphere.

Geometric Dilution of Precision (DOP). DOP occurs when there is no adequate cross cut in the "fix" (i.e. all satellites are all too closely located to each other). The consequence is that all of the signals are vulnerable to same errors from the atmosphere. Errors can occur in the horizontal (H), the vertical (V) and in time (T).

#### 3.6.2 Modes

With the exception of automated takeoff, the following modes may be engaged via the Taranis X9D controller as described in section 2.7. All settings are configurable via QGC. Position hold is the recommended flight mode for hand-flying. All flight modes are designed for operation with all motors functioning.

Caution: If any motor ceases functioning, land immediately.

Fully-automated (HOTL):

Mission: Vehicle executes a predefined mission/flight plan (https://docs.px4.io/master/en/flying/missions.html) that has been uploaded to the flight controller.

Return to Home: Ascend to safe altitude and return via a direct path to the home location.

Auto takeoff: Vehicle ascends to takeoff altitude and holds position. Triggered via QGC.

Auto land: Vehicle lands at the position where the mode was engaged.

Semi-automated (HITL):

Position Hold: RC mode where roll, pitch, throttle sticks control movement in corresponding axes/directions. Centered sticks level vehicle and hold it to fixed altitude and position against wind.

Altitude Hold: RC mode like Manual mode but with altitude stabilization (centered sticks level vehicle and hold it to fixed altitude). The horizontal position of the vehicle can move due to wind (or pre-existing momentum).

Non-automated:

Manual: RC mode where centered sticks level vehicle (only - position is not stabilized).

### 3.7 Battery Limitations

Use only 6S LiPo batteries with AS150 connectors. Consideration should be given to battery weight vs capacity if replacing the battery.

Battery capacity: 16000mAh

Maximum charge rate: 1C

Maximum discharge rate: 15C

Ambient temperature for battery charging: 0°C to 43°C.

Ambient temperature for battery discharging: 0°C to 60°C.

Warning: Battery exposure to temperatures greater than 60°C for extended periods of time (more than 30 minutes) may result in damage to the battery or a fire.

### 3.8 Range and Endurance Limitations

#### 3.8.1 Battery

The battery will nominally last approximately 25 minutes depending on flight conditions.

#### 3.8.2 Command and Control Link

The C2 link has a published range of 1.5km. Maintaining VLOS will likely require a reduced range.

## Section 4

## Hazards, Protections, and Warning systems

## Ref: 901.78 A manufacturer that has made a declaration to the Minister in respect of a model of remotely piloted aircraft system under section 901.76 shall make available to each owner of that model of system

### (c) a remotely piloted aircraft system operating manual that includes

- (v) the characteristics of the system that could result in severe injury to crew members during normal operations,
- (vi) the design features of the system, and their associated operations, that are intended to protect against injury to persons not involved in the operations,
- (vii) the warning information provided to the pilot in the event of a degradation in system performance that results in an unsafe system operation condition,

#### Table of contents

4.1 Introduction

4.2 Hazards to RPAS crew

4.3 Protections Against Injury to Uninvolved Personnel

4.4 Warnings and alerts

#### 4.1 Introduction

This section describes potential hazards to RPAS crewmembers, design features to protect against injury to persons not involved in RPAS operations, and the RPAS warning and alert systems.

#### 4.2 Hazards to RPAS crew

Electric shock: The maximum battery voltage is 25.2V which poses a minimal shock risk. The PDB is purposefully located at the center of the frame platform and is difficult to reach by hand, so the chance of accidental contact is remote. The battery should be checked for damage or swelling prior to each use, and never short-circuited.

Laceration: Crew members should not approach the RPA on the ground when armed for flight, or at all when motors are spinning. There is a loud buzzer to alert personnel that the drone is armed for flight and should not be approached. The RPA cannot be armed unless the safety switch has been pressed and held for approximately 2 seconds. If there is a preflight delay, the safety switch should be deactivated to prevent inadvertent arming or motor actuation.

Trauma injuries: Crew members should not approach the flightpath of the RPA unless necessary for an emergency or safety concern, and should never stand directly beneath it. Unless required, it is good practice to stay at least 5m laterally from the RPA.

Burns: Crew members should not mishandle the battery. Mishandling the battery can pose a fire risk. Puncturing, short circuiting, or exposing the battery to excessive ambient temperature could cause a fire. Mishandling the battery during charging by selecting the wrong battery type, failing to perform a balanced charge, or excessive charge rate could cause a fire.

Note: See Section 3.7 for battery limitations.

#### 4.3 Protections Against Injury to Uninvolved Personnel

Pterosoar is not intended to fly over or near people and must maintain 100 ft horizontal separation at any altitude from any non-crew member or person uninvolved in its operations.

The flight crew should include visual observers to ensure that uninvolved personal do not approach the flightpath or come within 100 ft of the RPA.

The RPA has configurable failsafe actions. Failsafe actions include: provide a warning, hover in place, return to home, or land in place. The following conditions can be specified to trigger a failsafe action:

Geofencing: Virtual regions within which the vehicle can fly, or in which it is not allowed to fly. The geofence regions are configurable in QGC. Breaching the fence triggers the failsafe action.

Low power: Battery level which triggers the failsafe action is configurable via QGC.

Lost link (C2 or Telemetry): Link loss timeout and failsafe action for either datalink are configurable via QGC.

#### 4.4 Warnings and Alerts

The primary warning system is through QGroundControl. The laptop base station will sound an audio alert and give a corresponding on-screen message of any system degradation. Alerts include but are not limited to low signal strength, low battery, non-responsive motor, GPS degradation, Pixhawk sensor degradation or failure, geofence alert, etc.

Types of alerts include:

Warning Alert: For conditions that require immediate pilot awareness and immediate response;

Caution Alert: For conditions that require immediate pilot awareness and subsequent response; and

Advisory Alert: For conditions that require pilot awareness and may require subsequent response.

Examples of marginal performance alerting includes:

GPS errors including GPS dilution of precision (DOP) when the geometries of available satellites does not provide sufficient coverage to meet navigation precision.

Navigation/Orientation errors such as Inertial Measurement Unit sensor faults/drifts.

Degradations in C2 link bandwidth and responsiveness cause by unknown or uncharacterized sources of interference, indicated by reduced or marginal RSSI.

Most warnings also appear on the screen of the Taranis X9D with corresponding audio cueing.

## Section 5

## Normal and Emergency Operating Procedures

### Ref: 901.78 A manufacturer that has made a declaration to the Minister in respect of a model of remotely piloted aircraft system under section 901.76 shall make available to each owner of that model of system

### (c) a remotely piloted aircraft system operating manual that includes

### (viii) procedures for operating the system in normal and emergency conditions

### See document “Normal and Emergency Procedures” as well as the pre-flight planning guide.

## Section 6

### Handling, Care and Maintenance

### Ref: 901.78 A manufacturer that has made a declaration to the Minister in respect of a model of remotely piloted aircraft system under section 901.76 shall make available to each owner of that model of system

(a) a maintenance program that includes

(i) instructions related to the servicing and maintenance of the system, and

(ii) an inspection program to maintain system readiness;

### (c) a remotely piloted aircraft system operating manual that includes

(ix) assembly and adjustment instructions for the system.

#### Table of contents

6.1 Introduction

6.2 Transport | Storage

6.3 Assembly | Disassembly

6.4 Cleaning and Care

6.4.1 Propeller Care

6.4.2 Battery Care, Storage, and Use

6.5 Scheduled Maintenance

6.5.1 Annual Inspection (example)

6.5.2 500 Hour Preventive Maintenance (example)

6.6 Other Field and/or Shop Maintenance

### 6.1 Introduction

This Section contains the recommended procedures for proper handling of the RPA. It also identifies certain inspection and maintenance requirements which should be followed if the RPA is to retain its original performance and dependability.

### 6.2 Transport | Storage

Pterosoar should be transported in its protective carrying case with sufficient padding. Propellers should be removed. It is recommended to tape off the positive terminal of the battery.

### 6.3 Assembly | Disassembly

The forward and rear motor arms are hinged and lock in the central position for storage, and in the deployed position for flight. The landing gear is hinged and locks in the downward position for flight operations. The propellers incorporate a DJI quick release mounting system and lock in place.

### 6.4 Cleaning and Care

The RPA can be cleaned with a soft cloth and isopropyl alcohol. Ensure the battery is disconnected and the RPA is powered off prior to cleaning.

#### 6.4.1 Propeller Care

Propellers must be checked before each flight for nicks or cracks and installed securely.

#### 6.4.2 Battery Care, Storage, and Use

The battery is charged using HT206 charger. Ensure LiPo battery type and balanced charge are selected. The maximum charge rate is 1C and discharge rate is 15C. Do not exceed 4.2V per cell. If the voltage is less than 3.3V in any cell, the battery must be replaced. For long term storage (over a week), the battery should be charged to 3.8V – 3.9V per cell.

### 6.5 Scheduled Maintenance

#### 6.5.1 Annual Inspection

Test all batteries for capacity.

Upgrade firmware and software to latest revisions.

#### 6.5.2 500 Hour Preventive Maintenance

Disassembly, inspection of components for wear, replace any components as required by manufacturer.

Test all motors and replace if necessary.

Test all batteries for capacity.

Upgrade firmware and software to latest revisions.

### 6.6 Other Field and/or Shop Maintenance

Either the Here3 GPS or the M8N SE100 GPS may be used. The Here3 plugs into either CANbus port of the Pixhawk. The M8N SE100 plugs into the GPS2 port and the I2C port of the Pixhawk.

## Section 7

### Supplements

#### Table of contents

7.1 General

7.2 Radio Payload

### 7.1 General

This Section contains information regarding optional equipment | payload | accessories which may be installed in the RPAS.

### 7.2 Radio Payload

Radio payload is still under development.

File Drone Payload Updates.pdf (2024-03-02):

## Drone Payload Updates

28 February 2024

## Contents

3.3.2 | Timer/counter compare match interrupt service routine (used to set chopping cadence)...9
3.3.3 | Timer/counter input capture interrupt service routine (used to read PWM pulse width) ....9

## 1 Introduction and current hardware

Until now, the PteroSoar drone radio payload has consisted of the following:

Signal source: Leo Bodnar mini precision GPS reference clock

1

Chopper: Analog Devices HMC545 RF switch eval board²

controlled by an Arduino Mega³

Battery: cellphone battery pack from Amazon with two USB-A outputs

Antenna: Aaronia BicoLog 5070⁴

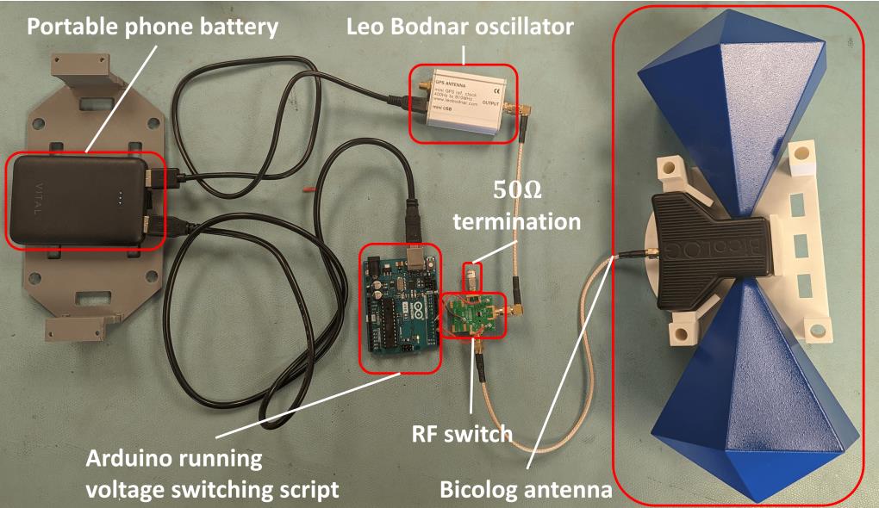
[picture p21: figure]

To switch from a steady-on state to a chopping state, it has been necessary to land the drone and manually change configuration. This is not desired as it needlessly drains battery in the descent to land and climbout back to pattern altitude during the calibration flight at the start of a series of mapping sorties.

The chopping script used on the Arduino has been a simple loop using timeouts to control the GPIO inputs to the HMC545 rf switch. This method of using timeouts is not very accurate, as the Arduino is not perfect at measuring time and the chopper can drift over even short flights. In addition, this setup is needlessly bulky and expensive:

Leo Bodnar cost: CAD $187.75¹

HMC545 eval board cost: CAD $188.68²

Arduino Mega cost: CAD $48.40³

## 2 New Hardware

### 2.1 Overview

Complexity, bulkiness, weight, and cost can be reduced by using a smaller Arduino and a clock generator controlled by the Arduino GPIO. The chopper can be made more accurate and chopping frequency drift minimized by using the internal timer/counter of the Arduino’s processor. Then, the chopping can be implemented by turning on and off the output of the clock generator at a cadence controlled by the timer/counter. There is no need for the RF switch in this configuration, only the Arduino and the clock generator chip. Moreover, by tying the drone’s X8R radio into the Arduino GPIO as an input, we can use the same timer/counter to read the PWM signal and implement radio control of the chopper state (steady on, chopping, or steady off).

In this configuration we have employed an Arduino (Abra) Nano⁵
controlling an Si5351 clock generator chip on a Mikroe-4113 eval board⁶
. Abra is a local electronics store and their Abra Nano is functionally the same as a stock Arduino Nano.

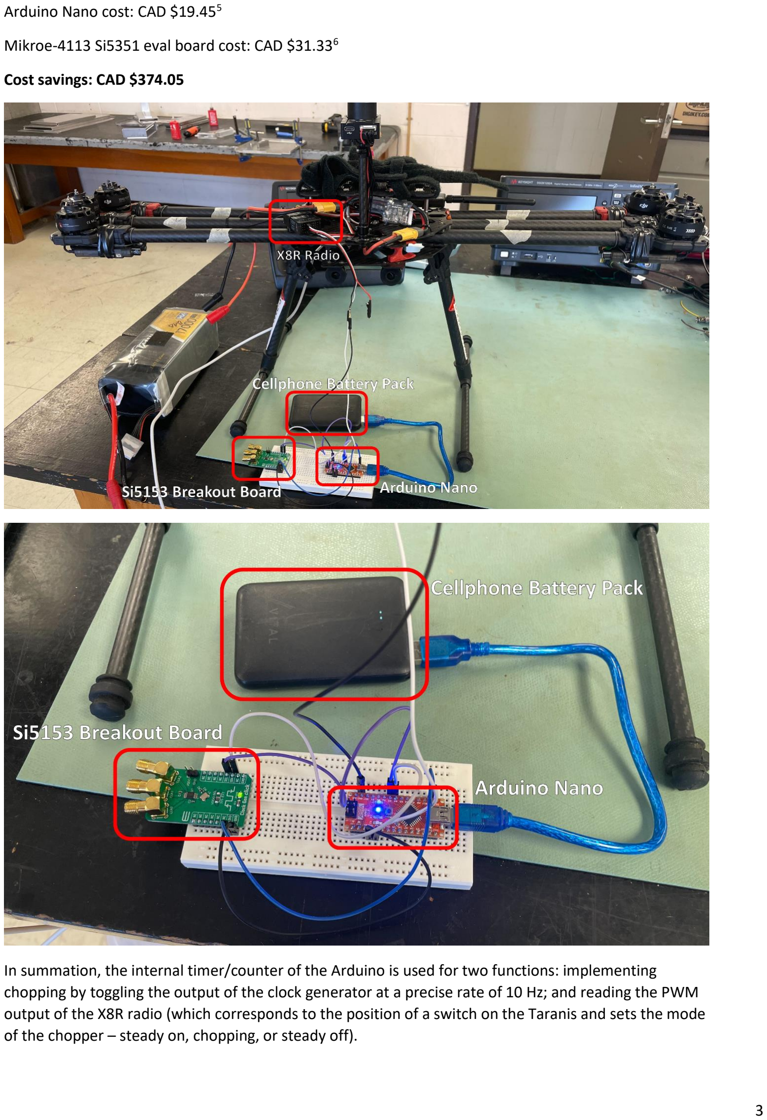
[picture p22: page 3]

Arduino Nano cost: CAD $19.45⁵

Mikroe-4113 Si5351 eval board cost: CAD $31.33⁶

Cost savings: CAD $374.05

In summation, the internal timer/counter of the Arduino is used for two functions: implementing chopping by toggling the output of the clock generator at a precise rate of 10 Hz; and reading the PWM output of the X8R radio (which corresponds to the position of a switch on the Taranis and sets the mode of the chopper – steady on, chopping, or steady off).

### 2.2 Wiring

The Si5153 is controlled via I2C and runs off of 3.3 V. The Arduino’s FTDI USB chip supplies enough current to power the Si5153. For power the 3V3 and GND pins of the Si5153 eval board are connected directly to the 3.3 V tap off of the Arduino and one of its ground pins. If this proves problematic when connected to load, a 3.3 V regulator will be easy to implement. The Arduino Nano’s I2C SDA and SCL pins are pins A4 and A5 by default, and these are wired directly to the SDA and SCL pins of the Si5153 eval board.

The signal and ground pins from output 6 of the X8R radio are connected to pin D8 (the default input capture interrupt pin for the Arduino’s timer/counter – more on that in a bit) and a ground pin, respectively. Output 6 is used because we are using channel 6 (Taranis switch D mapped to channel 6 in the Taranis “Mixes” config page). Channels 1-5 are used for drone control, so channels 6-8 are available for other uses such as the chopper.

Taranis “Mixes” config page, note CH6:

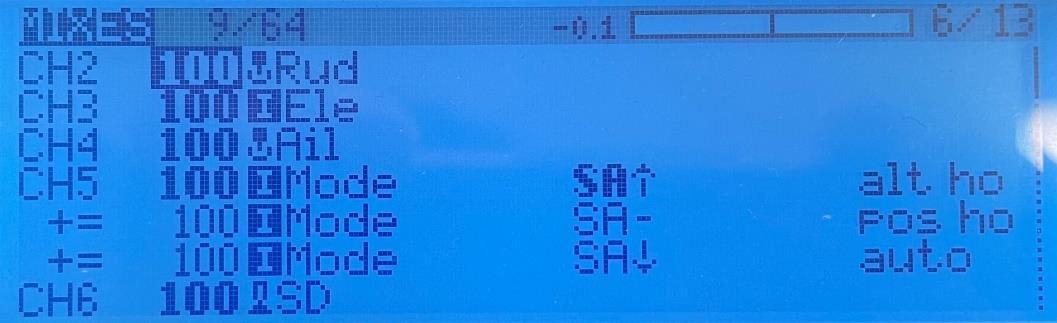
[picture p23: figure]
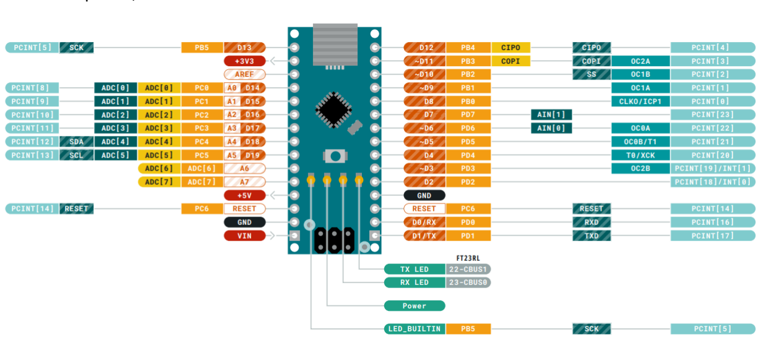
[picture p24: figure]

Arduino Nano pinout, for reference:


Here we can see the I2C SDA and SCL pins on A4 and A5. We can also see the pins concerning the timer/counter:

Output compare pins OC1A and OC1B on pins D9 and D10

Input capture pin ICP1 on D8

The 3.3 V tap off and ground pins are also easily identified.

## 3 Arduino code

### 3.1 Setting up the Si5153 clock generator

The Si5153 has two PLLs and three outputs. To have three different output frequencies, two outputs would need to share one of the PLLs.

Each PLL is set with a multiplier from the default clock speed of 25 MHz. Then each clock output can have two different dividers to set an output frequency.

In integer mode, the two PLL multipliers can have values of 15 to 90. The first clock divider (called multisynth divider) can have values of 4, 6, or 8. The second divider (called additional R divider) can have values of 1, 2, 4, 8, 16, 32, 64, 128. SiLabs recommends integer mode to avoid clock jitter, though fractional settings are also available.

SiLabs puts out some configuration software to help optimize the combinations of PLL multipliers, multisynth dividers, and R dividers for whatever set of output frequencies one desires.

There are two Arduino libraries for the Si5153: one from Adafruit⁷ (https://www.arduino.cc/reference/en/libraries/adafruit-si5351-library/)

, and one from Etherkit⁸ (https://www.arduino.cc/reference/en/libraries/etherkit-si5351/)
. The Adafruit
library gives a bit more intuitive low-level setting of the individual PLL multipliers and dividers. However, the Adafruit library doesn’t have individual on-off control of the three outputs – either all three are on or all three are off.

The Etherkit library does have the ability to set PLLs, but it is functionally “clunky” and is not designed with that kind of manipulation in mind. Instead, the user provides a frequency, and the library determines what multipliers and dividers are necessary to set the desired frequency. The library cautions that if the desire is to set the PLL multisynths and dividers, then the user must keep careful track of the settings to make sure valid multipliers and dividers are used.

Two advantages of the Etherkit library are the ability to turn on and off each of the three outputs individually, and the ability to set the power levels of the three outputs (drive strength from 2 mA or ~ 3 dBm to 8 mA or ~10 dBm, according to Etherkit). Currently, we are using the Etherkit library but the Adafruit version would be simple to implement.

The Si5153 manipulation in the Arduino code is simple. In the setup function, the chip is initialized, the frequency set, and all 3 outputs disabled. As described later, the output of clock 0 is then toggled continuously for chopping or set to on or off for the non-chopping modes.

### 3.2 Enabling and setting up the Arduino’s timer/counter

3.2.1 Timer/counter overview
The timer/counter is an integral part of the Atmel ATMega328p microcontroller that is the heart of the Arduino. Usage of this chip is well-documented in its data sheet⁹ (https://ww1.microchip.com/downloads/en/DeviceDoc/Atmel-7810-Automotive-Microcontrollers-ATmega328P_Datasheet.pdf)
. A timer counter increments at the clock speed of the processor, and in normal mode it overflows at its max value and starts over. We use a 16-bit timer-counter with a max value of 65535. Rather than normal mode, we use it in clear timer on compare mode. In this mode, the timer/counter increments to a preset maximum value, resets, and resumes counting. It can be configured to trigger an interrupt at the maximum value and execute a set of instructions. Prescalers for the clock can also be set, which divide down the clock speed to increment the counter at effectively a slower rate. This is useful if trying to time a longer period than would be possible by incrementing to the max value of 65535 at the Arduino’s clock speed of 16 MHz.

The Arduino has three timer/counters: 0 which is 8-bit, 1 which is 16-bit, and 2 which is 8-bit. We use timer/counter 1 as the 16 bits give finer control over the chopping frequency, and also timer/counter 1 is the only one of the three that has an input capture bit to use for PWM measurement. Section 15 of the data sheet⁹ describes timer/counter 1.

3.2.2 Setting the timer/counter registers
From the data sheet⁹
, there are two control registers for timer/counter 1 that need to be set: TCCR1A and TCCR1B. We also need to set register TIMSK1, the interrupt mask register. We use interrupts for both the 10 Hz chopping and the PWM measurement. We will also set the data direction register.

Both registers TCCR1A and TCCR1B contain waveform generation mode bits that must be set, described in the following table.


We want mode 4: clear timer on compare (CTC). It will count to its maximum value which we set in register OCR1A (output compare register). We could also use mode 12, but that uses the input capture register ICR1 for its maximum counter value. We want to use that register in measuring the PWM output of the drone’s X8R radio by having the PWM signal trigger an input capture interrupt, so we use mode 4 instead.

3.2.2.1 Setting timer/counter control register TCCR1A
From the datasheet⁹
, the bits of TCCR1A that we need to set are:

Bits WGM11 and WGM10 can be found in table 15-5 above. For mode 4 they are both set to 0. The remaining bits can be found in the following table:


We will toggle both OC1A and OC1B on compare match (i.e. when the timer/counter reaches its max value), just to have two outputs (on pins D9 and D10) should we ever want that. So, we set COM1A1 and COM1B1 to 0, and COM1A0 and COM1B0 to 1.

Thus, we set TCCR1A to a state of: B01010000.

3.2.2.2 Setting timer/counter control register TCCR1B
From the datasheet⁹
, the bits of TCCR1B that we need to set are:

Bit ICNC1 (input capture noise cancelling) can be set to 1 to filter inputs from the input capture pin. We haven’t needed it.

Bit ICES1 (input capture edge select) selects the mode of the input capture bit: falling edge (0) or rising edge (1). We use this bit in the X8R PWM output detection, described later.

Bits WGM13 and WGM12 can be found in table 15-5 above. For mode 4 they are set to 0 and 1, respectively.

Bits CS12, CS11, CS10 can be found in the following table:


Now, some math. I have been describing the chopper as being at 10 Hz. That is true, but we actually want the timer/counter to compare match at 20 Hz, as it toggles the output of the clock generator chip (the signal source) on and off at every compare match. Essentially the signal needs to be on for 0.05 seconds and off for 0.05 seconds for a 10 Hz chopping frequency; this gives a timer/counter frequency of 20 Hz since it is working in those chunks of 0.05 seconds. The Arduino clock frequency is 16 MHz. Trying to set that to 20 Hz yields a top value for the counter of 16E6 / 20 = 800,000. This is well over the maximum possible value of 65535. However, using a 1/64 clock prescaler yields a top value of (16E6 /
64) / 20 = 12500. This value is acceptable and 1/64 is the smallest prescaler that gives us a usable value (i.e. the best resolution). From benchtop measurements, a top value of 12508 most closely keeps a timer/counter overflow rate of 20 Hz. We set register OCR1A to this top value (see table 15-5). The top value of 12508 is off from the calculated value of 12500 (really 12499 due to how the timer/counter overflows). This is because the crystal oscillator of the Arduino is not precisely at 16 MHz; we measured its frequency to be 16.0114 MHz. The top count value should be tuned for the individual Arduino to set the appropriate timer/counter compare match frequency.

From the above table (15-6), for a 1/64 prescaler we set bits CS12, CS11, and CS10 to 0, 1, 1 respectively.

From all this, we set TCCR1B to an initial state of: B00001011.

3.2.2.3 Setting timer/counter interrupt mask register TIMSK1
From the datasheet⁹
, the bits of TIMSK1 that we need to set are:

We need to enable input capture interrupts, and output compare match A interrupts. These are bits ICIE1 and OCIE1A, respectively. The other bits are described in the datasheet but aren’t useful to us.

Thus, we set TIMSK1 to a state of: B00100010

3.2.2.4 Setting the data direction register DDRB
One final bitmask is set: the Data Direction Register. We want to set the data direction of the timer/counter outputs – OC1A and OC1B on pins 9 and 10. From the Arduino documentation¹⁰ (https://docs.arduino.cc/retired/hacking/software/PortManipulation/) , these
pins fall under Port B of the ATMega328p chip:


From the ATMega328p datasheet⁹ , DDRB maps as follows:

Thus, to set the data direction of pins 9 and 10 to output, we set DDRB to B00000110 (i.e. decimal 6). It is functionally the same as setting pinMode of pins 9 and 10 to output.

### 3.3 Setting the states of the chopper

3.3.1 Overview
As has been discussed, we desire three states of the chopper, corresponding to the three positions of switch D on the Taranis:

Steady on (up)

Chopping, 10 Hz (middle)

Steady off (down)

We use the timer/counter compare match interrupt service routine to set the chopping behavior. We use the timer/counter input capture interrupt service routine to measure the PWM pulse width of the X8R output signal, which corresponds to Taranis switch position.

3.3.2 Timer/counter compare match interrupt service routine (used to set chopping cadence) Setting the OCR1A register to 12508 with a 1/64 clock prescaler ensures that the timer/counter compare match interrupt happens at precisely 20 Hz. Within the compare match ISR, three global flags are used: on_flag, chop_flag, and off_flag. Only one of these Booleans is ever set to True at a time. When the interrupt happens and the ISR is triggered, one of three things will happen:

on_flag True: The output of clock 0 of the Si5351 eval board is enabled (only set when the ISR is first triggered after the on_flag is set to True, so that it is not being constantly re-enabled at 20 Hz).

chop_flag True: The output of clock 0 of the Si5351 eval board is toggled (i.e. if it was enabled, disables it and vice-versa). The output is off for one 20 Hz period and on for one 20 Hz period, giving a 10 Hz chopping period.

off_flag True: The output of clock 0 of the Si5351 eval board is disabled (only set when the ISR is first triggered after the off_flag is set to True, so that it is not being constantly re-disabled at 20 Hz).

The three flags are set in the main loop of the Arduino code according to the state of Taranis switch D, which is determined by reading the PWM output of the X8R radio.

3.3.3 Timer/counter input capture interrupt service routine (used to read PWM pulse width) The input capture ISR is triggered whenever a rising or falling edge is detected at the ICP1 input pin (Arduino pin D8). Bit ICES1 of TCCR1B selects rising or falling edge detection. Whenever a capture event occurs, the ICR1 register is updated with the current timer count. When a rising event is detected, marking the beginning of a pulse, we store the timer count value as read from ICR1. Bit ICES1 is also flipped to detect the upcoming falling edge of the pulse. When the falling edge is detected, marking the end of the pulse, we again store the timer count value; bit ICES1 is also flipped again, set up to detect the upcoming rising edge of the next pulse. By subtracting the timer count at the beginning of the pulse from the timer count at the end of the pulse, we obtain the pulse width in units of timer counts. Overflows are accounted for by adding the maximum timer count value (12508) to the falling edge count value in the event the rising edge count value is greater than the falling edge count value. When a pulse is measured, a flag is set telling the main loop to store the measured pulse width.

The three positions of Taranis switch D correspond to three different PWM pulse widths output from the X8R receiver (approximate values):

1 ms (Taranis switch D up – corresponds to “steady on”)

1.5 ms (Taranis switch D middle – corresponds to “chopping”)

2 ms (Taranis switch D down – corresponds to “steady off”)

As the Arduino’s clock is 16 MHz and we set the timer/counter with a 1/64 clock prescaler, these pulse widths correspond to timer counts of 250 (up), 375 (middle), and 500 (down). In practice we have measured count values of 247, 375, and 503. We think that these count values differ slightly from their calculated values due to measurements showing that the crystal oscillator of the Arduino does not have a frequency of precisely 16 MHz, and that the X8R PWM pulse widths are marginally off from the above time values. As all of these pulse widths are well below a 20 Hz period of .05 sec (i.e. maximum timer/counter value of 12508), we do not have to worry about multiple timer/counter overflows occurring in one pulse.

The main loop of the Arduino code detects the flag indicating a pulse has been measured. According to the measured pulse width (i.e. Taranis switch D position), it then sets the on_flag, chop_flag, and off_flag Booleans as appropriate, to be used in the compare match ISR.

## 4 Conclusion

Bench tests of this new payload seem to indicate a stable and usable output. We will fly it at Uapishka in March 2024 and report on any anomalous behavior.

## 5 References

1. Leo Bodnar:
https://www.leobodnar.com/shop/index.php?main_page=product_info&products_id=301
2. HMC545 eval board:
https://www.digikey.ca/en/products/detail/analog-devices-inc/EV1HMC545A/5403566
3. Arduino Mega:
https://www.digikey.ca/en/products/detail/arduino/A000067/2639006
4. Aaronia BicoLog:
https://aaronia.com/en/shop/radial-isotrope-antenne-bicolog-5070
5. Arduino (Abra) Nano:
https://abra-electronics.com/robotics-embedded-electronics/arduino-boards/abranano-abra-arduino-nano-v3.0-compatible-atmega328p.html (https://abra-electronics.com/robotics-embedded-electronics/arduino-boards/abranano-abra-arduino-nano-v3.0-compatible-atmega328p.html)
6. Mikroe-4113 Si5351 eval board: https://www.digikey.ca/en/products/detail/mikroelektronika/MIKROE-4113/12318588
7. Adafruit Si5351 Arduino library: https://www.arduino.cc/reference/en/libraries/adafruit-si5351-library/
8. Etherkit Si5351 Arduino library: https://www.arduino.cc/reference/en/libraries/etherkit-si5351/
9. ATMega328p datasheet, specifically section 15 for timer/counter 1: https://ww1.microchip.com/downloads/en/DeviceDoc/Atmel-7810-Automotive-Microcontrollers-ATmega328P_Datasheet.pdf (https://ww1.microchip.com/downloads/en/DeviceDoc/Atmel-7810-Automotive-Microcontrollers-ATmega328P_Datasheet.pdf)
10. Arduino port register documentation: https://docs.arduino.cc/retired/hacking/software/PortManipulation/

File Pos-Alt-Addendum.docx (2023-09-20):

Pterosoar Position and Altitude Verification – Addendum

Table of Contents

Section 1: Introduction

Section 2: Data and Analysis/Results

Section 1: Introduction

A new configuration for the Pterosoar GPS system has been developed, making use of dual u-blox F9P modules for GPS heading and position. This was motivated by the magnetic environment of the Arctic supplying insufficient signal to the drone’s magnetometer.

The new GPS modules are Helical models manufactured by Holybro. The same test methodology used with the Here3 GPS was used to confirm the lateral accuracy of the dual Holybro GPS system. GPS altitude accuracy was not measured as we have been using the barometric altimeter for altitude, which has not been altered.

Section 2: Data and Analysis/Results

The drone with the dual GPS system was hiked to 10 locations around the McGill downtown campus. At each location, the drone’s GPS position was checked against the position reported by Google Maps.


Pterosoar dual GPS position verification test locations

Data

Position Verification
Point # | Map lat | Map lon | GPS lat | GPS lon | GPS Error (m)
1 | 45.5070086 | -73.5785776 | 45.506963 | -73.5785979 | 5.3
2 | 45.5065575 | -73.5798866 | 45.506558 | -73.5798795 | 0.6
3 | 45.5059728 | -73.5790551 | 45.505962 | -73.5790614 | 1.3
4 | 45.5052980 | -73.5796894 | 45.505287 | -73.5796909 | 1.2
5 | 45.5043129 | -73.5772902 | 45.504301 | -73.5772899 | 1.3
6 | 45.5047340 | -73.5765070 | 45.504738 | -73.5765044 | 0.5
7 | 45.5038129 | -73.5748655 | 45.503818 | -73.5748693 | 0.6
8 | 45.5040460 | -73.5785455 | 45.504031 | -73.5785444 | 1.6
9 | 45.5051382 | -73.5789371 | 45.505096 | -73.5788923 | 5.8
10 | 45.5061288 | -73.5804230 | 45.506116 | -73.5804170 | 1.5

GPS position verification test data

Analysis/Results

GPS Position

GPS position error was determined by calculating the great-circle distance between the Google Maps position and the drone’s reported GPS position using the haversine formula.

The GPS position accuracy was measured to be, to a 95% confidence level, 2.0m +/- 1.4m.

The measured GPS position accuracy meets the 10m requirement of CAR 901.69, 901.76, and Standard 922.

Conclusion

Pterosoar has demonstrated that it’s lateral position accuracy with the dual GPS system meets and in fact surpasses the position requirements of the CARs and Standard 922. This report addendum will be kept on file in accordance with CAR 901.79.

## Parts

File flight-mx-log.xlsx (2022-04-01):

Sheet: Sheet1
Date | Location | Pilot | Other Crew | Takeoff Time (hh:mm) | Land Time (hh:mm) | Total Time | Remarks
2021-01-01 | Mojave Spaceport | Yeager, C | Picard, J.L.; Hughes, H. | 15:00:00 | 16:03:00 | 1.1 | Test

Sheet: Sheet2
Date | Name | Manufacturer | Model
Description/Instructions
Date | Name | Manufacturer | Model
Description/Instructions
Date | Name | Manufacturer | Model
Description/Instructions
Date | Name | Manufacturer | Model
Description/Instructions
Date | Name | Manufacturer | Model
Description/Instructions
Date | Name | Manufacturer | Model
Description/Instructions
Date | Name | Manufacturer | Model
Description/Instructions
Date | Name | Manufacturer | Model
Description/Instructions

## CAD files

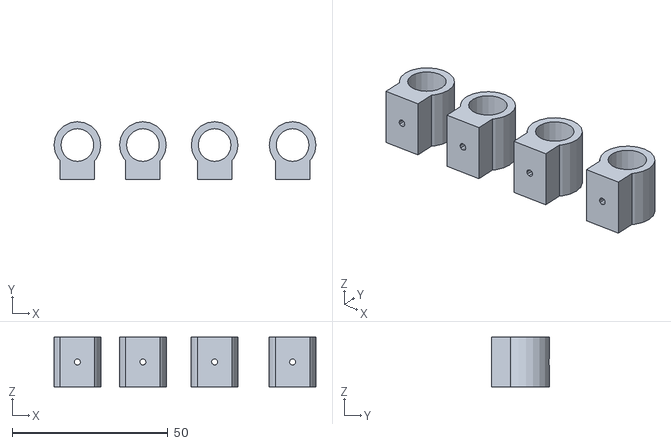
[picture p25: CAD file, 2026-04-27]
drone_stls/Dual GPS F9P cf_tubing_clips.stl
84.0 x 18.5 x 16.0

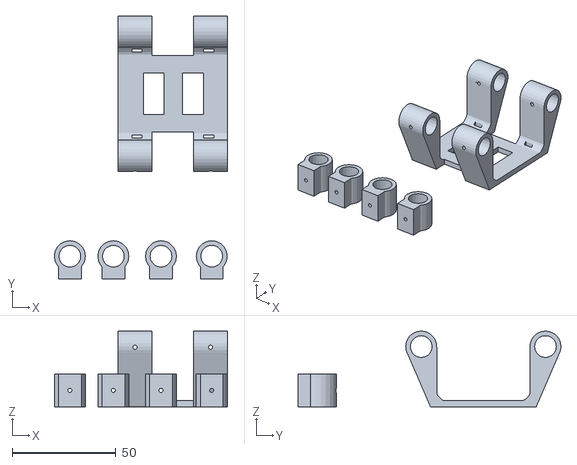
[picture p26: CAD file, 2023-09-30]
DroneGPSMountingSys.stl
83.7 x 127.0 x 36.6

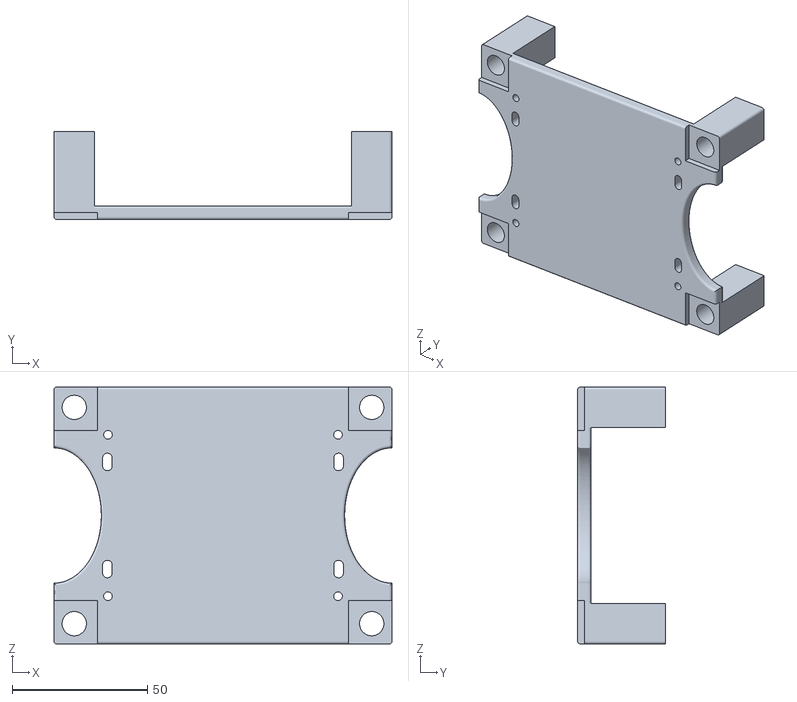
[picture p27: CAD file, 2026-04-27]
drone_stls/payload mount - Payload_Module_v5 (bicolog cutouts).STL
125.0 x 32.5 x 95.0

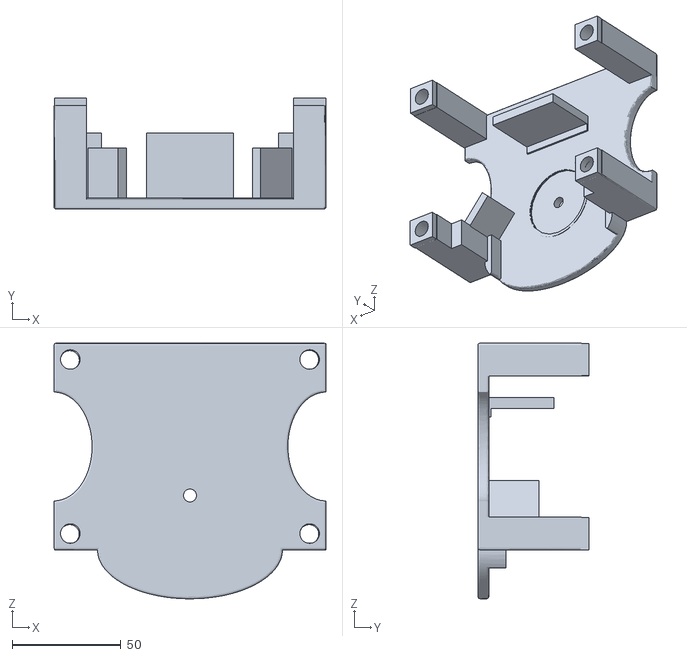
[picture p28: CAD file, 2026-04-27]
drone_stls/payload mount - Bicolog mount 2.0.stl
125.0 x 51.1 x 117.5

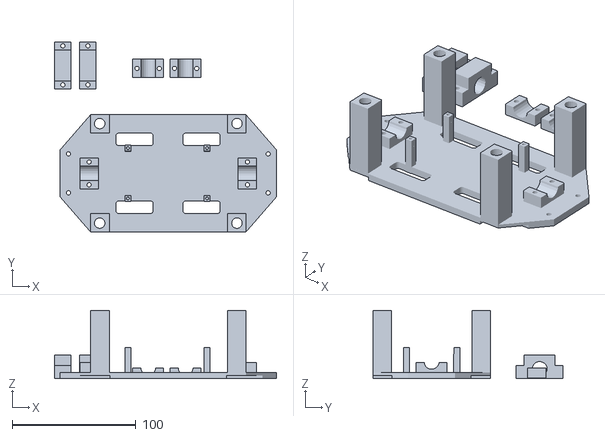
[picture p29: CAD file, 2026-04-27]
drone_stls/dipole mount.stl
179.5 x 153.9 x 55.0

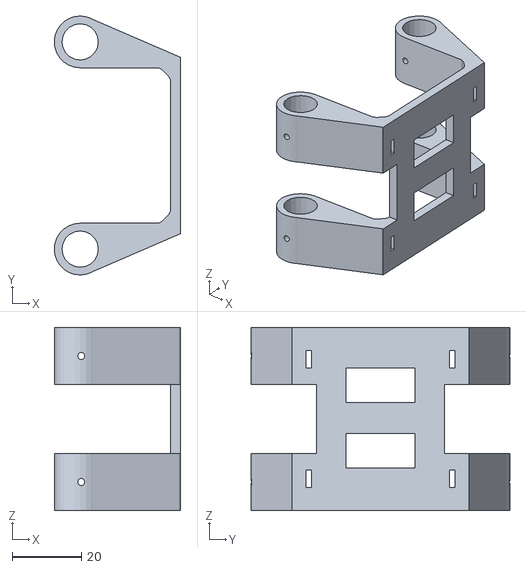
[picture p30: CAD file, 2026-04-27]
drone_stls/Dual GPS F9P mount.stl
36.6 x 75.0 x 53.0

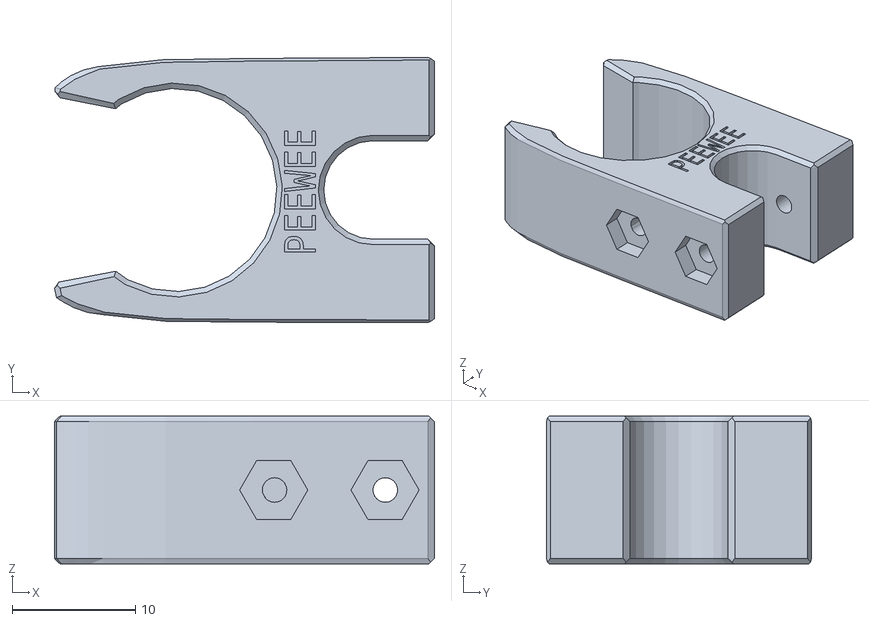
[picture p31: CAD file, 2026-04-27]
drone_stls/drone arm clip.stl
30.9 x 21.6 x 12.0

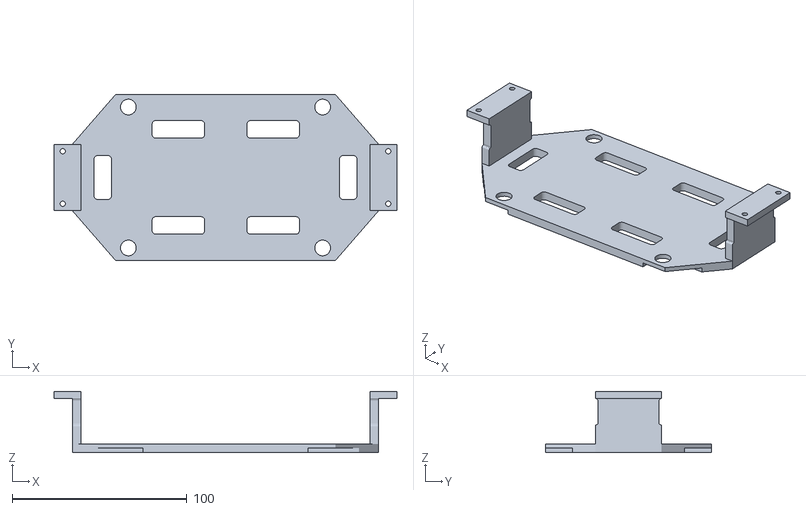
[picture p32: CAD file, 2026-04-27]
drone_stls/payload mount - top plate.stl
196.0 x 95.0 x 35.0

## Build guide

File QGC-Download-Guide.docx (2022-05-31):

QGroundControl Installation for Windows

Table of Contents

Section 1: QGroundControl Download and Installation

Section 2: Mission Planner Download and Installation

Section 1: QGroundControl Download

The flight software/graphical interface used for the operation of Pterosoar is QGroundControl (QGC). QGC supports two flight stacks namely PX4 and Ardupilot, for the purposes of Pterosoar, PX4 is currently being used however, both flight stacks are supported by the cube orange flight controller.

When initially running the newest version of the QGC installer (https://docs.qgroundcontrol.com/master/en/getting_started/download_and_install.html), Windows security doesn't recognize the publisher and tries to block the download, simply ignore the security message and run the installer. While installing the software various prompts asking to download missing drivers will appear, accept, and download all of these.

Once QGC is installed and opened test the drivers by connecting the drone via a USB port, if mission mode is automatically triggered there is no need to download any of the following software and QGC should be ready to function. If after waiting a few seconds QGC does not connect or an error message occurs stating the device is not recognized, unplug the drone and follow the steps in Section 2.

Section 2: Mission Planner Download

Mission Planner is a similar graphical interface that supports both Ardupilot and PX4 but is older than QGC. Mission Planner will in no way be used for the drone and is only being downloaded for the drivers it installs automatically. The Mission Planner installer (https://ardupilot.org/planner/docs/mission-planner-installation.html) will run similarly to the QGC installer and will also trigger the Windows security error. Accept all driver downloads when running the installer (this is the most important part), when the software is fully installed, completely close Mission Planner. Avoid opening Mission Planner while running QGC as the drone connection will be recognized by both software's.

To verify that the drone will now properly connect, close and reopen QGC. Connect the drone via USB cable once more and wait for it to boot up. After a few seconds QGC should recognize it and automatically connect. The software is now ready to be used.

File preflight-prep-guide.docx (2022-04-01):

Pre-Flight Preparation Guide
Item | Requirements
Documentation | Easily accessible during operation: | Drone Registration Certificate (901.09) Drone Pilot Certificate / Proof of Recency (901.57, 901.66)
| Immediately available and reviewed prior to flight: | Normal Operating Procedures (901.23) Emergency Procedures (901.23)
| Immediately available: | Operating Manual (901.30, see 901.78)
Fitness of Crew Members | May not act as crew if (901.27): - suffering or is likely to suffer from fatigue - otherwise unfit to perform properly the person’s duties - within 12 hours after consuming an alcoholic beverage - while under the influence of alcohol - while using any drug that impairs the person’s faculties to the extent that aviation safety or the safety of any person is endangered or likely to be endangered

Pre-flight Planning

A pilot of a remotely piloted aircraft shall, before commencing a flight, be familiar with the available information that is relevant to the intended flight (901.24)

- consider relevant NOTAMS
- consider relevant weather:
- must be able to maintain visual LOS (901.34)
- ensure that there is a sufficient amount of fuel or energy for safe completion of the flight (901.28)
- ensure that the drone and all equipment required by regulation is serviceable (901.29)
- determine the maximum distance from the pilot the aircraft can travel without endangering aviation safety or the safety of any person (901.28)
- consider the distance of the intended flight to any aerodrome (901.47, 901.73)

Ensure that each crew member, before acting as a crew member, has been instructed (901.28):

- with respect to the duties that the crew member is to perform
- on the location and use of any emergency equipment associated with the operation of the remotely piloted aircraft system

If flying in controlled airspace (req advanced license), file with Nav Canada (901.14, 901.71)

Site Survey

Take into account (901.27):

- the boundaries of the area of operation
- the type of airspace and the applicable regulatory requirements
- the altitudes and routes to be used on the approach to and departure from the area of operation
- the proximity of manned aircraft operations
- the proximity of aerodromes, airports and heliports
- the location and height of obstacles, including wires, masts, buildings, cell phone towers and wind turbines
- the predominant weather and environmental conditions for the area of operation
- the horizontal distances from persons not involved in the operation

Ensure, before take-off, launch, approach, landing or recovery (901.33):

- there is no likelihood of collision with another aircraft, person or obstacle
- the site set aside for take-off, launch, landing or recovery, as the case may be, is suitable for the intended operation

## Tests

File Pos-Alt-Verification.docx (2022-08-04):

Pterosoar Position and Altitude Verification

Table of Contents

Section 1: Introduction

Section 2: Regulatory References

Section 3: Test Methodology, Data, and Analysis/Results

Section 1: Introduction

Pterosoar is intended for operations at McGill University, which is within the CYUL Class C airspace. As a result, for compliance with the CARs and Standard 922 (relevant sections included in Section 2), position and altitude verification testing were conducted. Test methodology and results are presented in Section 3. Pterosoar has demonstrated that it meets the position and accuracy requirements outlined in the CARs and Standard 922.

This verification testing was conducted using the Here3 GPS. Pterosoar has the option of using the add-on RTK base station from Here that is designed to work with the Here3. No modifications to the drone itself are required for RTK mode. In RTK mode, Here states a GPS accuracy improvement of two orders of magnitude over the standard Here3.

Section 2: Regulatory References

CARs

901.69 (1) Subject to subsection (2), no pilot shall operate a remotely piloted aircraft system under this Division to conduct any of the following operations unless a declaration under section 901.76 has been made in respect of that model of system and the certificate of registration issued in respect of the aircraft specifies the operations for which the declaration was made:

(a) operations in controlled airspace;

(b) operations at a distance of less than 100 feet (30 m) but not less than 16.4 feet (5 m) from another person except from a crew member or other person involved in the operation, measured horizontally and at any altitude; or

(c) operations at a distance of less than 16.4 feet (5 m) from another person, measured horizontally and at any altitude.

901.76 (1) For each model of remotely piloted aircraft system that is intended to conduct any of the operations referred to in subsection 901.69(1), the manufacturer shall provide the Minister with a declaration in accordance with subsection (2), except in the case of a model referred to in subsection 901.69(2) and that is intended to conduct any of the operations referred to in that subsection.

(2) The manufacturer’s declaration shall

(a) specify the manufacturer of the remotely piloted aircraft system, the model of the system, the maximum take-off weight of the aircraft, the operations referred to in subsection 901.69(1) that the aircraft is intended to undertake and the category of aircraft, such as a fixed-wing aircraft, rotary-wing aircraft, hybrid aircraft or lighter-than-air aircraft;

(b) indicate that the manufacturer

(i) declares that it meets the documentation requirements set out in section 901.78, and

(ii) has verified that the system meets the technical requirements set out in Standard 922 — RPAS Safety Assurance applicable to the operations referred to in subsection 901.69(1) for which the declaration was made.

(3) The manufacturer’s declaration is invalid if

(a) the Minister has determined that the model of remotely piloted aircraft system does not meet the technical requirements set out in the standard referred to in subparagraph (2)(b)(ii); or

(b) the manufacturer has notified the Minister of an issue related to the design of the model under section 901.77.

901.79 (1) A manufacturer that has made a declaration to the Minister in respect of a model of remotely piloted aircraft system under section 901.76 shall keep, and make available to the Minister on request,

(a) a current record of all mandatory actions in respect of the system; and

(b) a current record of the results of, and the reports related to, the verifications that the manufacturer has undertaken to ensure that the model of the system meets the technical requirements set out in the standard referred to in subparagraph 901.76(2)(b)(ii) applicable to the operations for which the declaration was made.

(2) The manufacturer shall keep the records referred to in subsection (1) for the greater of

(a) two years following the date that manufacturing of that model of remotely piloted aircraft system permanently ceases, and

(b) the lifetime of the remotely piloted aircraft that is an element of the model of system referred to in paragraph (a).

Standard 922 – RPAS Safety Assurance

922.04 Operations in Controlled Airspace

Information Note: These technical requirements are applicable to RPAS declarations for operations referred to in paragraph 901.69(1)(a) of the CARs.

Information Note: The required accuracy for operations within controlled airspace is identified for purposes of communications with other users of the airspace (e.g. control tower) in order to provide a minimum confidence related to the altitude and position reports from an RPAS pilot.

#### Required Accuracy

(1) The remotely piloted aircraft system must have a lateral position accuracy of at least +/- 10 m while operating within the controlled airspace.

(2) The remotely piloted aircraft system must have an altitude accuracy of at least +/- 16 m while operating within the controlled airspace.

Advisory Circular 922-01: Remotely Piloted Aircraft Systems Safety Assurance

6.1 Operations in controlled airspace

(1) General. For RPAS operating in controlled airspace CAR Standard 922.04 (https://tc.canada.ca/en/corporate-services/acts-regulations/list-regulations/canadian-aviation-regulations-sor-96-433/standards/standard-922-rpas-safety-assur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) requires that design requirements are met to allow for communication of position and altitude to air traffic controllers and other participant aircraft with the specified level of accuracy. While it is acknowledged that accuracy requirements alone do not provide any additional robustness or system reliability objectives, the intent is to provide a minimum required accuracy for position and altitude such that other users of the airspace are accurately made aware of any potential hazard the RPA may pose.

(2) Position Accuracy. A system position accuracy of +/-10m has been identified as the minimum accuracy for position within controlled airspace. Most modern Global Navigation Satellite System (GNSS) technologies can easily achieve this accuracy nearly 100% of the time. Considerations should be taken to ensure that this accuracy can be maintained while in degraded modes of operation, and in all portions of the proposed operational space (e.g. considerations for buildings, trees, valleys etc.). The accuracy should be clearly identified in the limitations portions of the operating manual.

(3) Altitude Accuracy. A system altitude accuracy of +/- 16m has been identified as the minimum accuracy for altitude within controlled airspace. Most modern GNSS technology can achieve this accuracy using the WGS-84 geodetic datum. Consideration should be taken when designing altitude measurement systems that differences between ground level, sea level, and various geodetic datum are taken into account.

(4) Errors. Accuracy is a probabilistic measurement based on assumptions related to the quality and integrity in a constantly changing environment. It is important to understand the errors that may contribute to degradation of accuracy and take these into account as part of the overall design error budget. Examples of sources of errors adversely affecting accuracy are identified below.

(a) Terrain Errors. GNSS signals are also subject to errors caused by the terrain. Terrain masking of the signal, for example by a building or mountain, blocks the antenna on the RPAS from receiving the satellite signal. A GNSS signal reflected by the landscape such that the receiver now receives "additional" signals which can create confusion and may need to be processed out to avoid creating position errors.

(b) Atmospheric Errors. Atmospheric errors are caused by the Ionosphere and the Troposphere, which are both capable of refracting GNSS radio signals. Ionospheric Density is diurnally dependent, which means that it varies with time of day (or night). The density is affected by, among other factors, humidity, temperature and pressure. These variations adversely affects the "signal speed x time" equation built into GNSS position calculations. To correct for these errors, a number of steps are taken. Troposphere errors can be caused by moisture absorbing/refracting signal and cause errors up to 6m. Ionosphere errors can be caused by the atmospheric refraction of the GNSS signals and may be up to 40-60 m by day and 6-12 m at night. These errors can be mitigated by the use of multi-frequency receivers, selection of masking angle, and/or the use of augmentation systems (either ground-based, such as Local Area Augmentation System [LAAS], or space-based, such as European Geostationary Navigation Overlay Service [EGNOS]).

(c) Satellite Errors. These are errors resulting from poor or unexpected geometries related to the positions of the GNSS satellites in reference to an RPAS. Gravitational effects of the Sun and Moon may pull the SV from planned orbital path. Solar Radiation creates EMI prior to the signal hitting the atmosphere.

(d) Geometric Dilution of Precision (DOP). DOP occurs when there is no adequate cross cut in the "fix" (i.e. all satellites are all too closely located to each other). The consequence is that all of the signals are vulnerable to same errors from the atmosphere. Errors can occur in the horizontal (H), the vertical (V) and in time (T).

Section 3: Test Methodology, Data, and Analysis/Results

Test Methodology

Pterosoar was hand-carried to 13 locations at the McGill downtown campus and up Mount Royal, see the below map outlining the test points. At each location, the GPS position, GPS altitude, and barometric altitude were recorded.

GPS position was checked against Google maps, and altitudes were checked against a topographic map of Montreal located at https://en-ca.topographic-map.com/maps/fwea/Montreal/. This topographic map uses a data set published in Geophysical Research Letters Volume 44, 2017.¹

The test points covered an altitude band of 501ft, which exceeds the 400ft AGL altitude limitation for RPAS.

Note: GPS altitude is the MSL altitude. The Pterosoar flight controller reports barometric altitude relative to where the flight controller was powered on.

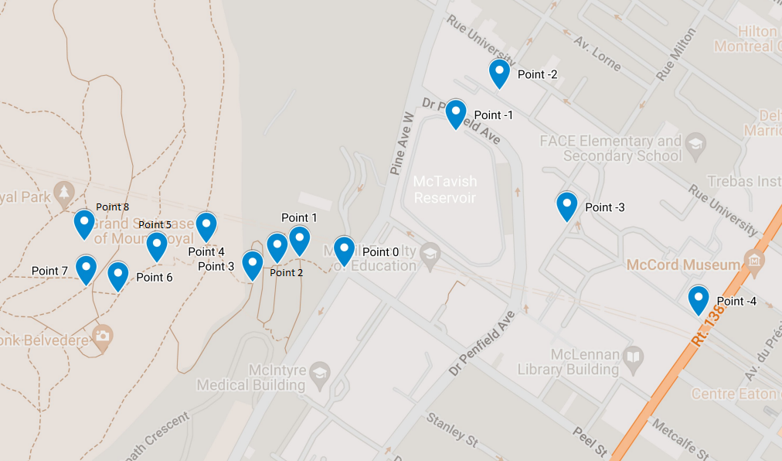
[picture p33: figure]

Pterosoar GPS/altitude verification test locations

Data

Position and altitude verification test data is presented in the below tables.

Position Verification
Point # | Map lat | Map long | GPS lat | GPS long | GPS Error (m)
-4 | 45.50388 | -73.57485 | 45.50393 | -73.57495 | 9.8
-3 | 45.50522 | -73.57748 | 45.50514 | -73.57730 | 16.6
-2 | 45.50710 | -73.57889 | 45.50712 | -73.57901 | 9.6
-1 | 45.50651 | -73.57974 | 45.50654 | -73.57963 | 9.2
0 | 45.50457 | -73.58200 | 45.50458 | -73.58194 | 4.8
1 | 45.50472 | -73.58290 | 45.50475 | -73.58288 | 3.7
2 | 45.50462 | -73.58335 | 45.50455 | -73.58332 | 8.1
3 | 45.50437 | -73.58385 | 45.50432 | -73.58378 | 7.8
4 | 45.50492 | -73.58478 | 45.50500 | -73.58483 | 9.7
5 | 45.50464 | -73.58578 | 45.50458 | -73.58585 | 8.6
6 | 45.50422 | -73.58657 | 45.50417 | -73.58658 | 5.6
7 | 45.50430 | -73.58716 | 45.50424 | -73.58710 | 8.2
8 | 45.50496 | -73.58725 | 45.50495 | -73.58736 | 8.7

GPS position verification test data

Altitude Verification
Point # | Map alt (m, MSL) | GPS alt (m, MSL) | GPS alt error (m) | Map relative alt (m) | Baralt relative alt (m) | Baralt error (m)
-4 | 54 | 58.2 | 4.2 | -46 | -52.8 | 6.8
-3 | 61 | 60.8 | 0.2 | -39 | -44.2 | 5.2
-2 | 70 | 71.6 | 1.6 | -30 | -36.5 | 6.5
-1 | 76 | 76.3 | 0.3 | -24 | -22.9 | 1.1
0 | 100 | 100.9 | 0.9 | 30 | 37.7 | 7.7
1 | 111 | 111.6 | 0.6 | 41 | 54.4 | 13.4
2 | 118 | 118.7 | 0.7 | 48 | 58.9 | 10.9
3 | 122 | 122.1 | 0.1 | 52 | 69.1 | 17.1
4 | 140 | 142.6 | 2.6 | 70 | 83.2 | 13.2
5 | 167 | 172.4 | 5.4 | 97 | 123.7 | 26.7
6 | 193 | 193.6 | 0.6 | 123 | 138.6 | 15.6
7 | 199 | 201.6 | 2.6 | 129 | 143.4 | 14.4
8 | 207 | 206.4 | 0.6 | 137 | 150.7 | 13.7

GPS and barometric altitude verification data

Analysis/Results

GPS Position

GPS position error was calculated by the great-circle distance between the map data point and the GPS data point using the haversine formula.

Data point -3 was taken directly in front of the Arts building at the McGill downtown campus. It is likely that terrain masking as discussed in AC922-01 (and presented in Section 2) in the form of buildings blocking the GPS signal occurred.

Removing data point -3 due to the poor GPS environment, the GPS position accuracy was measured to be, to a 95% confidence level, 7.8m +/- 1.3m.

The measured GPS position error meets the 10m requirement of CAR 901.69, 901.76, and Standard 922.

Points -4, -2, and 4 also have relatively high GPS position errors. Point -4 is located at the McGill downtown main gate on Rue Sherbrooke and point -2 is located adjacent to the Rutherford physics building at the McGill downtown campus; both are in a somewhat similarly poor GPS environment to point -3 (but do have better sky visibility). Point 4 is directly next to the Mount Royal grand staircase, located on a nearly sheer cliff-face of the mountain. Terrain masking was likely occurring at these points. The need to consider terrain masking of the GPS signal is included in the Pterosoar operations manual as a result of this testing.

GPS Altitude

GPS altitude error was calculated by the difference between the map altitude and the GPS altitude.

The average GPS altitude error was measured to be, to a 95% confidence level, 1.6m +/- 1.0m.

The measured GPS altitude error meets the 16m requirement of CAR 901.69, 901.76, and Standard 922.

Barometric Altitude

Barometric altitude error was calculated by the difference between the map relative altitude and the barometric relative altitude

The average barometric altitude error was measured to be, to a 95% confidence level, 11.6m +/- 3.9m.

The measured barometric altitude error meets the 16m requirement of CAR 901.69, 901.76, and Standard 922.

Note: For points -4, -3, -2, -1: the flight controller was reset at point 0, so the map and barometric relative altitudes are relative to point 0.

For points 0 to 8: the flight controller was reset at point -2, so the map and barometric relative altitudes are relative to point -2.

Points -4 to -1 have lower errors than the remaining points. These points were re-taken at the end of testing due to data quality concerns, and the flight controller (and baralt) was reset at point 0. These points were measured over a short time period of approximately 20 minutes. The other data points were measured during a climb up Mount Royal over approximately 2 hours. It is likely that the local barometric pressure (i.e. the local altimeter setting) was changing over the 2 hour period of points 0 to 8, but would not have changed as much during the 20 minute period of points -4 to -1. As a result, there is lower error for points -4 to -1. The Pterosoar operations manual includes a note to update the QNH barometric altimeter parameter or cycle flight controller power prior to each flight during extended operations as a result of this testing.

Point 5 appears anomalous (as does data point 3 to a lesser degree; the same analysis applies). It is possible a gust of wind affected the flight controller’s MS5611 barometric pressure sensor, or there may have been a momentary lapse of the sensor. Removing point 5 as an anomalous data point, the barometric altimeter error was measured to be, to a 95% confidence level, 10.5m +/- 3.1m. This meets the 16m requirement of CAR 901.69, 901.76, and Standard 922.

Conclusions

Pterosoar has demonstrated that it meets and in fact surpasses the position and altitude requirements of the CARs and Standard 922. This report will be kept on file in accordance with CAR 901.79.

1. Yamazaki D., D. Ikeshima, R. Tawatari, T. Yamaguchi, F. O'Loughlin, J.C. Neal, C.C. Sampson, S. Kanae & P.D. Bates. A high accuracy map of global terrain elevations. Geophysical Research Letters, vol.44, pp.5844-5853, 2017. https://agupubs.onlinelibrary.wiley.com/doi/full/10.1002/2017GL072874

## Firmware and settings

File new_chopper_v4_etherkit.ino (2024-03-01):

// Arduino (Abra) Nano control of Si5351 clockgen chip on a MIKROE-4113 eval board
// Reads drone's X8R radio PWM output signal to control chopper state (steady off, chopping, steady on)
// Eval board uses 3.3 V power
// I2C SDA on pin A4
// I2C SCL on pin A5
// ATMega328p timer/counter 1 overflow output on pins D9 and D10
// GPIO output from chopper routine on pin D6 and built in LED
// X8R PWM input as a timer/counter 1 input capture interrupt on pin D8

#include "si5351.h"
#include "Wire.h"
#include <util/atomic.h>

Si5351 si5351;

const int test_lead = 6; // toggle GPIO according to the mode of the chopper, could be useful for a LED or something.
const uint16_t count_top = 12508; // counter timer overflow value, must be less than 32k for the input capture overflow method to work, 12508 is for 10 Hz chopping with a 1/64 prescaler (Arduino clock speed 16 MHz)

// variables and flag used in the timer/counter input capture interrupt ISR (PWM reading) (I know 'interrupt ISR' is a bit redundant but wanted to be clear):
uint8_t lowval; // used to read lowest 8 bits of input capture register
uint8_t highval; // used to read highest 8 bits of input capture register
uint16_t falling; // timer count at the falling edge of the PWM signal
uint16_t rising; // timer count at the rising edge of the PWM signal
volatile uint16_t interval; // number of counts between rise and fall of PWM signal ie the pulse width in timer counts
boolean dataflag; // flag that indicates a PWM pulse has been measured

// flags used in the timer/counter compare match interrupt ISR (10 Hz chopping):
boolean toggle0; // used in the chopping routine to toggle the output off and on
boolean chop_flag; // sets chopper state to chopping if true
boolean on_flag; // sets chopper state to steady on if true
boolean on_init; // flag so that the on state is only set when the Taranis switch is first flipped and not continuously reset at 20 Hz
boolean off_flag; // sets chopper state to steady off if true
boolean off_init; // flag so that the off state is only set when the Taranis switch is first flipped and not continuously reset at 20 Hz

// variables used in the main loop
const uint16_t up_pwm = 247; // timer/counter interval (PWM pulse width) of Taranis switch up position
const uint16_t middle_pwm = 375; // timer/counter interval (PWM pulse width) of Taranis switch middle position
const uint16_t down_pwm = 503; // timer/counter interval (PWM pusle width) of Taranis switch down position
const uint16_t pwm_range = 5; // range around detected PWM intervals to determine a match
uint16_t oldPWM; // used in main loop to detect a change in PWM pulse width ie mode of the chopper
uint16_t PWM; // same as above

void setup() {
  // configure GPIO
  pinMode(test_lead, OUTPUT);
  pinMode(LED_BUILTIN, OUTPUT);

  // configure Si5351 clockgen
  bool i2c_found;
  Serial.begin(9600);
    /* Initialise the sensor */
  i2c_found = si5351.init(SI5351_CRYSTAL_LOAD_8PF, 0, 0);
  if(!i2c_found)
  {
    Serial.println("Device not found on I2C bus!");
  }
  Serial.println("OK!");
  // Set CLK0 to output 50 MHz, all outputs disabled for now
  si5351.set_freq(5000000000ULL, SI5351_CLK0);
  si5351.output_enable(SI5351_CLK0, 0);
  si5351.output_enable(SI5351_CLK1, 0);
  si5351.output_enable(SI5351_CLK2, 0);

  // configure timer/counter 1 and set interrupts
  TCCR1B = B00000000; // Stop Timer/Counter1 clock by setting the clock source to none.
  TCCR1A = B00000000; // Set Timer/Counter1 to normal mode.
  TCNT1  = 0; // Set Timer/Counter1 to 0
  OCR1A = count_top; // Set the Output Compare A for Timer/Counter1
  TCCR1A = B01010000; // Set Timer/Counter1 to CTC mode. Set OC1A and OC1B to toggle.
  TCCR1B = B00001011; // Start Timer/Counter1 clock by setting the source to CPU source. Set prescalar to 1/64.
  TIMSK1 = B00100010; // enable compare match interrupt and input capture interrupt
  DDRB = 6; // set data direction to output in case we want to get the raw clock output. Output on pins 9 and 10 (set in TCCR1A).
}

ISR(TIMER1_COMPA_vect) { // timer/counter 1 overflow interrupt, 10 Hz chopping freq or 20 Hz interrupt rate
  sei();
  if (chop_flag) { // chopping
    on_init = 0; // reset the init flags of the other modes
    off_init = 0;
    if (toggle0) {
      si5351.output_enable(SI5351_CLK0, 1); // enable signal output
      digitalWrite(test_lead, HIGH);
      digitalWrite(LED_BUILTIN, HIGH);
      toggle0 = 0; // reset chopper toggle
    } else {
      si5351.output_enable(SI5351_CLK0, 0); // disable signal output
      digitalWrite(test_lead, LOW);
      digitalWrite(LED_BUILTIN, LOW);
      toggle0 = 1; // set chopper toggle
    }    
  } else if (on_flag) { // steady on
    if (on_init == 0) { // only set this config on the initial Taranis switch setting and not re-set it at 20 Hz
      on_init = 1; // set init flags
      off_init = 0;
      si5351.output_enable(SI5351_CLK0, 1); // enable signal output
      digitalWrite(test_lead, HIGH);
      digitalWrite(LED_BUILTIN, HIGH);
    }    
  } else if (off_flag) { // steady off
    if (off_init == 0) { // only set this config on the initial Taranis switch setting and not re-set it at 20 Hz
      off_init = 1; // set init flags
      on_init = 0;
      si5351.output_enable(SI5351_CLK0, 0); // disable signal output
      digitalWrite(test_lead, LOW);
      digitalWrite(LED_BUILTIN, LOW);
    }    
  }
  cli();
}

ISR(TIMER1_CAPT_vect) {// timer/counter 1 input capture interrupt to read the PWM output of the X8R radio (channel 6 right now)
  if (not bit_is_set(TCCR1B, ICES1)) { // falling edge
    lowval = ICR1L; // get counter value
    highval = ICR1H;
    falling = lowval | highval << 8;
    if (rising > falling) { // if an overflow happened between rising and falling
      falling += count_top; // wrapping;
    }
    interval = falling - rising; // calculate the interval
    dataflag = 1; // tell the loop there's data
  }
  else { // rising edge
    lowval = ICR1L; // get counter value
    highval = ICR1H;
    rising = lowval | highval << 8;
    dataflag = 0; // need to wait for falling edge
  }
  TCCR1B ^= bit(ICES1); // in either case, flip the rising/falling edge detect bit
}

void loop() {
  // put your main code here, to run repeatedly:
  // read chopper state from X8R PWM output
  if (dataflag) { // a PWM pulse has been detected and pulse width measured
    ATOMIC_BLOCK(ATOMIC_RESTORESTATE) { // atomic read from the input capture ISR to avoid any register update errors
      PWM = interval;
    }
  } 
  if((PWM>oldPWM?PWM-oldPWM:oldPWM-PWM) > 2*pwm_range) { // subtract the smaller value from the larger value of PWM vs oldPWM. If the difference is more than a few counts then the PWM value changed - print it
    oldPWM = PWM;
    Serial.println(PWM);
  }

  // set chopper state flags according to X8R PWM output
  if((PWM > down_pwm - pwm_range) && (PWM < down_pwm + pwm_range)) { // down position of Taranis switch D
    // steady OFF
    off_flag = 1;
    on_flag = 0;
    chop_flag = 0;
  } else if ((PWM > middle_pwm - pwm_range) && (PWM < middle_pwm + pwm_range)) { // middle position of Taranis switch D
    // ON, Chopping
    chop_flag = 1;
    on_flag = 0;
    off_flag = 0;
  } else if ((PWM > up_pwm - pwm_range) && (PWM < up_pwm + pwm_range)) { // up position of Taranis switch D
    // steady ON
    on_flag = 1;
    off_flag = 0;
    chop_flag = 0;
  }
}

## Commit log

2023-09-30 .stl file for 3D printed dual GPS mount.
    [DroneGPSMountingSys.stl]
2024-03-01 Adding new Arduino chopper code and documentation
2024-03-02 mild fix to PWM values
2026-04-27 add drone stl files
    add drone stl files
    [Dual GPS F9P mount.stl, dipole mount.stl, drone arm clip.stl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]
2026-04-27 Rename Dual_F9P_GPS_cf_tubing_clips.stl to Dual GPS F9P cf_tubing_clips.stl
    [Dual GPS F9P cf_tubing_clips.stl]
